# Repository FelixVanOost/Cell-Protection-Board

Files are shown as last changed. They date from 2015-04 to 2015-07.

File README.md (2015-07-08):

Copyright Felix van Oost 2015.
This documentation describes Open Hardware and is licensed under the CERN OHL v1.2. You may redistribute and modify this documentation under the terms of the [CERN OHL v1.2](http://ohwr.org/cernohl). This documentation is distributed WITHOUT ANY EXPRESS OR IMPLIED WARRANTY, INCLUDING OF MERCHANTABILITY, SATISFACTORY QUALITY AND FITNESS FOR A PARTICULAR PURPOSE. Please see the CERN OHL v1.2 for applicable conditions.

# Cell-Protection-Board
A PCB to link the cell voltage taps of 8 parallel 6S batteries and protect them using fuses.

This project is developed by the [Electric Car Club](http://ubcelectriccar.com/) at the University of British Columbia, whose current goal is to break the world record for the fastest 1/4 mile in a street-legal electric car. The car, named Elektra, is a modified 1963 Volkswagen Beetle.

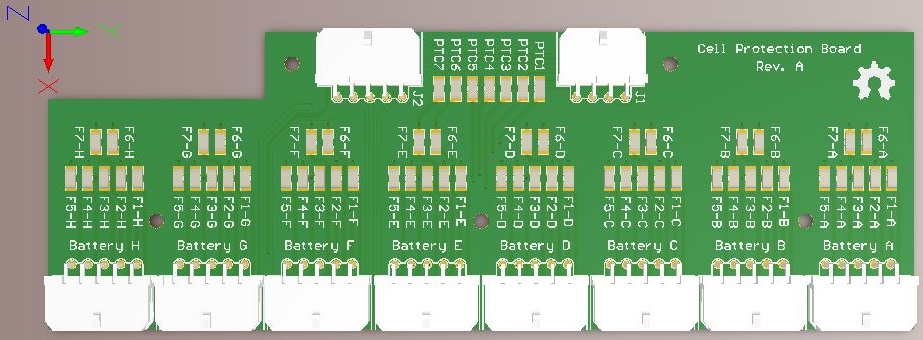
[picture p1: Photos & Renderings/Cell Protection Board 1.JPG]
Image of Cell Protection Board

*Cell Protection Board - Rev. A*

----------
Context
----------

Phase I of Elektras' battery pack consists of 30 [Turnigy 22.2V 6S 5Ah](http://www.hobbyking.com/hobbyking/store/__38515__Turnigy_Heavy_Duty_Series_5000mAh_6S_60C_Lipo_Pack.html) lithium-ion polymer batteries (originally designed for use in R/C airplanes) arranged in 5 series modules of 6 parallel batteries each. This results in a total nominal pack voltage of 111V with a peak discharge current of around 2,400A. Phase II (a future upgrade) will increase the number of parallel batteries in each module from 6 to 8 and the number of modules from 5 to 8 (resulting in a pack capable of around 3,000A peak discharge current at a nominal 177V).

The battery management system (BMS) incorporated into the car monitors the voltage of the individual cells within each battery in the pack and is capable of balancing cells with one another to maintain optimal battery health over time. This is accomplished through the connection of cell voltage taps, which are wired by the battery manufacturer between the cells in every battery. Each of the 6S batteries features 7 cell taps for monitoring and balancing purposes, which are seperate from the positive and negative leads of the battery and do not provide traction power to the car.

Since the 6 batteries in each module (Phase I) are connected together in parallel through copper bussbars, their cell voltage taps will also need to be paralleled together. In this way, the BMS can treat cell 1 from each of the 6 batteries as one large cell, followed by cell 2 and so on. The BMS will therefore only see 6 virtual cells arranged in series, regardless of how many batteries are actually connected together in parallel. One important consideration when connecting cell taps in parallel is that they provide an opportunity for excess current to flow between cells in the event that a cell in one battery fails short. This can cause cascading failures in the adjacent cells connected in that parallel group, which would cause significamt damage to the battery pack. To prevent such a failure from occuring, fuses can be placed along the cell taps to prevent excess current from flowing if a cell fails short.

Cell voltage taps play a key component in maintaining battery health over time, as they enable the individual cells to be balanced with one another periodically to accomodate for minuscule variations in chemistry and cell construction. Cell balancing is handled by the BMS, which dissipates excess energy in cells with higher voltage to bring them down to the same voltage as the other cells within the battery (this is done towards the end of the charging phase). The [Orion BMS](http://www.orionbms.com/) used in Elekta is capable of sustaining a maximum cell balancing current of around 200mA. Excess current flowing through the cell taps (as in the case where a cell fails short) will damage the BMS, however, so the inputs to the unit should also be fused for protection.

The Orion BMS is also capable of monitoring temperature data from up to 80 thermistors, thereby enabling it to take appropriate action if any battery exceeds a certain temperature threshold. In Elektra, a thermistor is fixed to each Turnigy battery within the overall pack (30 for Phase I).

----------
Functionality
----------

The Cell Protection Board performs four main functions:

- Connects the cell taps of 8 Turnigy 6S batteries in parallel. The 8 slots enable the board to accomodate the future Phase II battery pack, although only 6 slots will be populated during Phase I.
- Places fuses in series with each cell tap to protect adjacent parallel cells in the event that one cell in the group fails short. The fuses are designed to limit current in each cell tap to 3A, which will prevent the cells from overdischarging and avoid fusing or burning the 22AWG cell tap wires.
- Places PTC fuses in series with each cell tap input to the BMS. These are specified to trip at 250mA (50% above the rated Orion BMS balancing current), which should adequately protect the BMS without interfering with its normal operation.
- Outputs the 8 thermistor connections (one for each of the 8 batteries) to a single connector and links the grounds of all the thermistors together. This significantly reduces the amount of wiring needed between the battery pack and the BMS, making both installation and troubleshooting far simpler.

A Cell Protection Board is required for each series module in the battery pack (5 for Phase I). The board has been designed with space-efficiency in mind, so surface-mount fuses / PTCs and double-row connectors are used to minimise its total surface area. This also greatly reduces the cost of the boards and components, but comes at the expense of replaceability (a blown fuse will need to be desoldered and another one resoldered in its place). All surface-mount components are 3216 (metric) size, which provides a good balance between space-efficiency and ease of replacement. Nonetheless, the fastest and most efficient way to assemble the board is by reflow soldering, which produces consistent and excellent quality joints (a solder paste stencil file is included in the Gerber Files folder). Molex Micro-Grid connectors are used throughout the design due to their high current rating, compact footprint, and sturdy locking mechanism.

The Cell Protection Boards are designed to be modular - they can be easily modified to accomodate more or fewer batteries with a varying number of cells. Their functionality is also quite generic, enabling them to be used with almost any BMS solution or lithium-ion cell chemistry. Mounting holes are placed throughout the board to allow vertical stacking using standoffs.

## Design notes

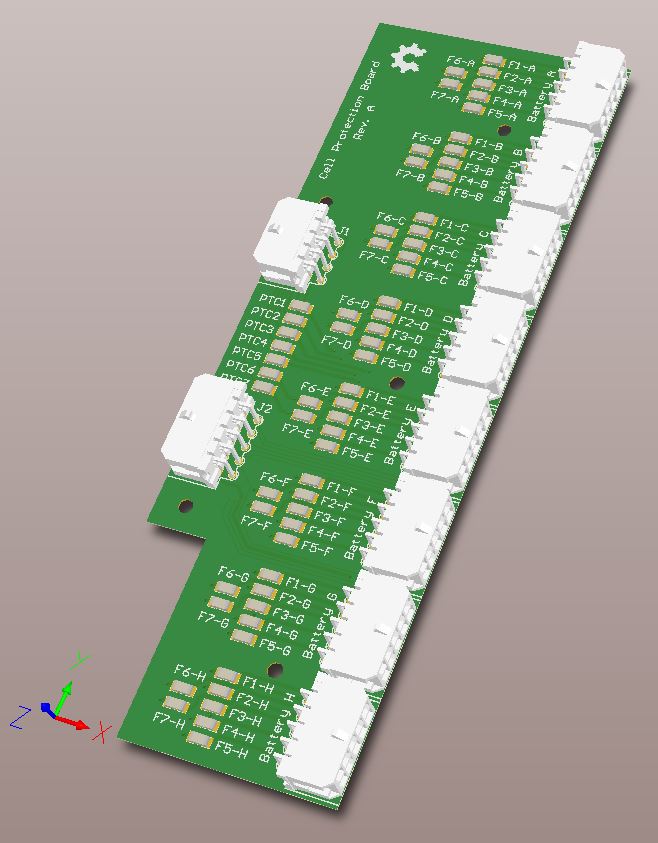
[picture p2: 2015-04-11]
Photos & Renderings/Cell Protection Board 2.JPG

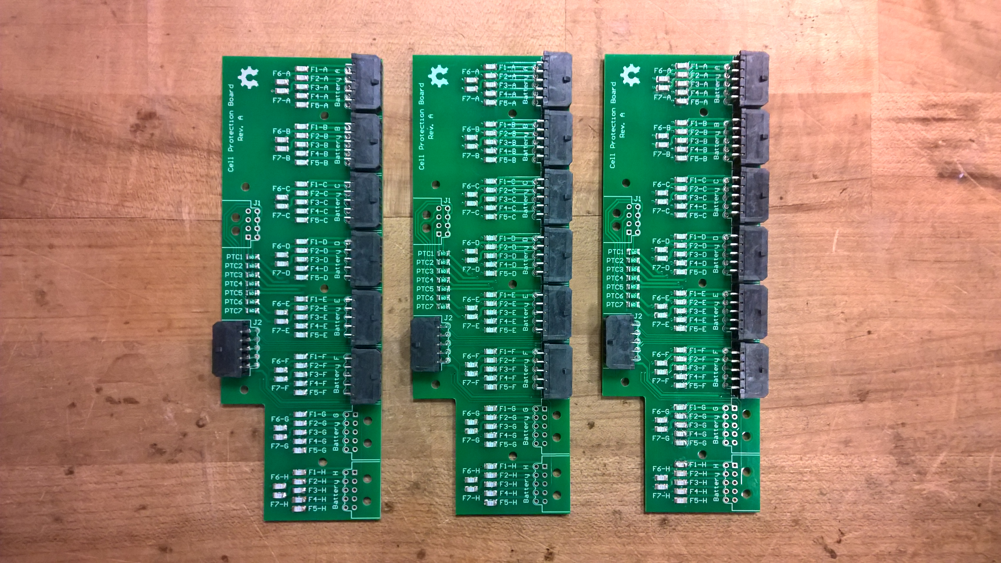
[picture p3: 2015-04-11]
Photos & Renderings/Cell Protection Board 3.jpg

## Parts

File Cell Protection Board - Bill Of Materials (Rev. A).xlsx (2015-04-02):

Part | Package | Digi-Key Part # | Qty. | Price (Each) | Price (Tot.) | Designator
Molex Micro-Fit 43045-Series 8-Pin Male Header | - | WM1816-ND | 1 | $2.83 | $2.83 | J1
Molex Micro-Fit 43045-Series 10-Pin Male Header | - | WM1817-ND | 9 | $2.83 | $25.47 | Battery A - Battery G, J2
Molex Micro-Fit 43025-Series 8-Pin Female Connector | - | WM1786-ND | 1 | $0.76 | $0.76 | -
Molex Micro-Fit 43025-Series 10-Pin Female Connector |  | WM1787-ND | 9 | $0.93 | $8.37 | -
Molex Micro-Fit 43030-Series 20-24AWG Tin Crimp Contact | - | WM1837CT-ND | 88 | $0.12 | $10.47 | -
Bel Fuse C1T-Series 3A Slow Blow Fuse | 3216 | 507-1896-1-ND | 56 | $0.34 | $19.26 | F1-A - F7-H
Bel Fuse 0ZCJ-Serise 250mA PTC Fuse | 3216 | 507-1794-1-ND | 7 | $0.16 | $1.12 | PTC1 - PTC7
 |  |  |  |  | $68.29

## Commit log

2015-04-02 Added Rev. A Gerber Files
    Includes complete files for printing the board and cutting a solder
    paste stencil.
2015-04-02 Added Rev. A Altium Designer FIles
    Includes PCB and circuit schematic files, PCB and schematic component
    libraries, and CAM output files.
    [Cell Protection Board.PcbDoc, Cell Protection Board.PcbLib, Cell Protection Board.PrjPcb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]
2015-04-02 Added Rev. A Bill Of Materials
    [Cell Protection Board - Bill Of Materials (Rev. A).xlsx]
2015-04-04 Added CERN OHL v1.2 license information
    [Cell Protection Board.SchDoc]
2015-04-11 Added photo and 3D renderings of board
2015-04-11 Update README.md
    Added 3D rendering of Cell Protection Board
